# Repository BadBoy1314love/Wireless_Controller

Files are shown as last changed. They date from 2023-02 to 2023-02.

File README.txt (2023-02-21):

/*******************************************/
/         以下为程序思路整理
/*******************************************/

继电器任务应该由多个输入信号对应单个任务
继电器任务输出应该由单个任务输出一个或多个IO
而不是多个任务共同占用一个IO

一个任务：
输入触发信号（一个或者多个信号）--->启动指定的任务
--->输出一个或者多个信号（应该由一个任务占用这些输出信号）
（不能由其他任务占用这些输出信号）

设置项
首先设置触发信号
设置不同的IO触发任务号（每个IO有其对应的任务）

继电器任务模式：
1.点动模式：
	有触发信号（无松手检测），则有输出，否则没有
2.自锁模式：
	有带松手检测触发信号，则启动任务输出，
	再次触发，则关闭输出
3.时间区间间歇：
	有带松手检测触发信号，则启动任务输出，
	再次触发，则关闭输出
	可以设置时间区间
	可以设置输出ON的时间，可按百分比设置
	可以设置输出OFF的时间，可按百分比设置
	可以设置周期时间
	可以设置OVERTIME，任务运行超过此时间则关闭
	
	“间歇”：应该有三个要素（以秒（S）作为时间单位）
	运行的时间，停止的时间，总的时间（周期时间Cycle Time）
	_______________
	               |_______________
	|<--On Time -->|<--Off Time-->|
	|<--------Cycle Time--------->|
	
	应该确认什么时候开始运行也就是起始运行时间，
	得确认两个起始时间，一个是On状态的起始时间，还有一个是Off状态的起始时间
	一共有两个状态，一个是On状态，一个是Off状态
	在指定的时间区间内将状态设置为On或者Off
	也就是做时间区间内判断
	
继电器的任务输出：
	首先当前任务TASK1是启动的状态，并且有了一个输出
	通过这个输出结果TASK1_Out,值为1则输出已经为当前任务分配的IO
	值为0则不输出
	
为什么外部输入信号触发的是任务，而不是任务内的具体信号？
如果没有外部输入设备，则可以使用ec11内部的Start Task

任务的触发
1.自锁触发，按下按键，并且释放才触发，端口匹配的任务

自锁触发的过程
1.确认端口为输入模式并且为自锁模式且端口被拉低，则记录下端口
2.判断有哪些端口被记录，再次判断端口有没有被释放，被释放则用端口任务号赋给自锁任务号
3.匹配到自锁任务号则开启或者关闭匹配的任务

2.点动触发，按下按键，直接触发端口匹配的任务

按键为松开状态此时按下则记录

点动触发的过程
1.确认端口为输入模式并且按键为松开状态，端口被拉低，则直接记录下端口，按键状态变为按下
2.判断有哪些端口被记录，再次判断端口是不是点动触发型，
  是则立即将端口任务号赋给点动任务号，然后如果端口被释放，
  则将按键设置为松开状态，允许重新设置

自锁还是点动输入实际模拟外部输入
自锁：按下按键，记录下按下的按键，进入记录的按键，直到按键释放，才设置任务
立即：按下按键，直接设置任务，并且直到按键释放才可重新设置

任务的时间控制:
首先是判断当前时间在时间区间内
再判断超时计数器有没有大于超时时间

否则任务的运行不满足时间条件
1,当前时间不在时间区间内，没有超时
//当前关闭输出
//直到在时间区间，继续运行

2.当前时间不在时间区间内，已经超时
//如果开启超时自动复位，将复位计数,否则关闭task，复位时间计数器，关闭输出

3.当前时间在时间区间内，已经超时
//如果开启超时自动复位，将复位计数，否则关闭task，复位时间计数器，关闭输出

如果要实现无限时间运行（意味着超时自动复位）

/******************************************************************************/
// STA模式操作步骤
/******************************************************************************/

AT+CWMODE_DEF=3        //设置当前wifi模式并保存到flash /1:STA/2:AP/3.STA+AP
AT+CWMODE_CUR=3  //设置当前wifi模式不保存到flash

AT+CWJAP_DEF="wifiname","password"   //连接AP并保存到FLASH
AT+CWJAP_CUR="wifiname","password"   //连接AP不保存到FLASH

AT+CIFSR                    //查看路由器分配的IP

AT+CIPMUX=1         //设置多连接 

AT+CIPSERVER=1,9527   //设置TCP服务器 

/*STA+AP模式设置*/
AT+CWMODE_CUR=3
AT+CWJAP_CUR="TP-LINK_847A","asdfghjkl"
AT+CWSAP_CUR="Wireless_Controller_Test","asdfghjkl",11,4
AT+CIFSR
AT+CIPMUX=1
AT+CIPSERVER=1,9527

/*GET 苏宁时间网址*/（get网址之后一定要加、/r/n）
AT+CIPMUX=0
AT+CIPSTART="TCP","quan.suning.com",80
AT+CIPSTART="TCP","223.111.230.101",80
AT+CIPSEND=50
GET http://quan.suning.com/getSysTime.do

/*GET www.shijian.cc 网址的GMT+8标准时间 */（get网址之后一定要加、/r/n）
AT+CIPMUX=0
AT+CIPSTART="TCP","www.shijian.cc",80
AT+CIPSTART="TCP","118.112.250.193",80
AT+CIPSEND=50
GET http://www.shijian.cc/000/clock.asp

/*GET www.beijing-time.org 网址上的GMT+8标准时间*/（get网址之后一定要加、/r/n）
AT+CIPMUX=0
AT+CIPSTART="TCP","beijing-time.org",80
AT+CIPSEND=50
GET http://www.beijing-time.org/t/time.asp
GET http://beijing-time.org/t/time.asp

GET /t/time.asp

/*http://api.k780.com/?app=life.time&appkey=10003&sign=b59bc3ef6191eb9f747dd4e83c99f2a4&format=json
*/

/*ESP8266的其他指令*/

AT+CIPSEND

AT+RESTORE   //重置

/*设置 UART 配置，保存到 Flash*/
AT+UART_DEF(_CUR)=9600,8,1,0,0

/*8266的初始化过程*/

AT+RST    //复位8266模块
AT+CWMODE_CUR=3   //设置当前wifi模式  
AT+CWJAP_CUR="TP-LINK_847A","asdfghjkl"   //连接AP

/*获取网络时间*/
AT+CIPSTART="TCP","www.shijian.cc",80
AT+CIPSEND=42
GET http://www.shijian.cc/000/clock.asp\r\n\r\n
显示时间

AT+CIPMUX=1   //使能多连接
AT+CIPSERVER=1,9527  //开启TCP服务器，只能在多连接的情况下开启
AT+CWSAP_CUR=\"Wireless_Controller\",\"asdfghjkl\",3,4  //设置8266 SOFTAP
AT+CIFSR

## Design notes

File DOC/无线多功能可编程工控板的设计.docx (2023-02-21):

江苏省无锡交通高等职业技术学校

毕 业 论 文

无线多功能可编程工控板的设计

学 院 | 机电工程学院
专 业 | 机电一体化
班 级 | 161321
姓 名 | 张淼垚
学 号 | 160332014
指导教师 | 蒋甜
起讫日期 | XXXX.XX～XXXX.XX

无线多功能可编程工控板的设计

# 摘 要

进入21世纪后，互联网技术获得了飞速的发展，随着传感器技术的发展，物联网技术也相继而生。

人们的生活水平获得了极大的提高的同时，人们对生活的要求也相应的提高了，为了获得更加优质的生活，获得智能化的生活，人们采用了物联网技术来提高生活质量。为了实现多功能的物联网控制，为了极大的便利生活，在生活中解放双手，在家庭中实现通用控制。

受到工业中常用的稳定可靠的PLC的影响，为了设计一种稳定可靠的便于在家庭中使用的多功能无线控制器，本文将讲诉STC89C52RC单片机为核心的一种低成本、时间准时、小型化无线多功能可编程工控板的设计。

关键词：物联网，传感器，多功能通用，无线，控制器，PLC

# 第一章 物联网的介绍

## 1.1 物联网的定义

物联网是指通过各种传感器将万物互联的互联网，是在互联网的基础上发展而来，物联网是将各种信息传感设备与网络的相结合从而形成的巨大网络，实现了在任意时间，任意地点，人与物与机的互联互通。

## 1.2 物联网的工作原理

通过各种信息传感器，例如射频识别、红外传感、激光扫描、全球定位等各种装置，实现采集例如声、光、热、电、力等各种信息，通过网络连接，实现，物与物，物与人之间的连接，实现对物品的智能化识别管理，整个过程是智能化的。

## 1.3 物联网的益处

通过物联网可以获得的最大好处是能够提高社会的智能化，自动化的水平，把原来不能实现的难以实现的功能实现了。通过给没有智慧的物体植入无线智能芯片，让人类的的感知更加灵敏，更加宽广，使得控制更加自如，让生活更加方便。

# 第二章 传感元件及动力元件

## 2.1 传感器原理及应用举例

### 2.1.1 主动式红外传感器

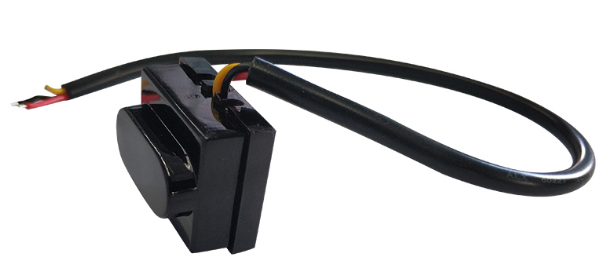
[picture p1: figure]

图2-1 主动式红外传感器实物图

主动式红外传感器是一种智能的非接触开关，利用红外光对物体的漫反射原理，当人或者物体进入感应器的感应区域，感应器将输出信号，人或物体离开后将停止输出，一般应用场景为水龙头阀门的感应开启与关断。

一般有高低电平输出方式以及NPN输出方式。

高低电平输出方式只提供一个高低电平信号，适用于小电流控制大电流，控制外部电路，MCU信号的识别与判断等，硬件连接示意图如图（2-2）。

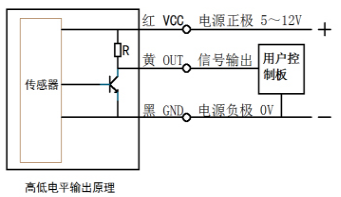
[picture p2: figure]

图2-2 高低电平原理图及接线图

NPN输出方式，当传感器输出断开时处于无电压的悬空状态，可以通过上拉电阻接到VCC的输出电压，当传感器输出闭合时电压为０V，即对０V（电源负极）导通，硬件连接示意图如图（2-3）。

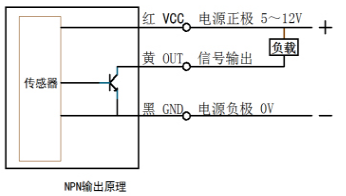
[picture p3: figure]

图2-3 NPN输出原理图及接线图

### 2.1.2 霍尔开关传感器

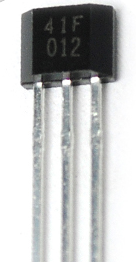
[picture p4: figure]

图2-4 霍尔开关传感器实物图

一般由电压调整器，霍尔电压发生器，差分放大器，施密特触发器，温度补偿电路和集电极开路的输出级组成的的磁敏传感电路，由半导体集成技术制造而成，一般输入为一个磁感应强度，输出是一个电压数字信号。

该传感器具有体积小，灵敏度高，响应速度快，温度性能好，精确度高，可靠性高等优点，应用场景一般为无触点开关，位置，转速检测与控制，报警装置。

### 2.1.3 光敏传感器

图2-5 光敏电阻器实物图

光敏电阻的工作原理是基于内光电效应。随着光照强度的升高，电阻值迅速降低，由于光照产生的载流子都参与导电，在外加电场的作用下作漂移运动，电子奔向电源的正极，空穴奔向电源的负极，从而使光敏电阻器的阻值迅速下降。在无光照时，几乎呈高阻状态，暗电阻很大。

基于光敏电阻器的工作原理于是有了光敏电阻传感器模块。

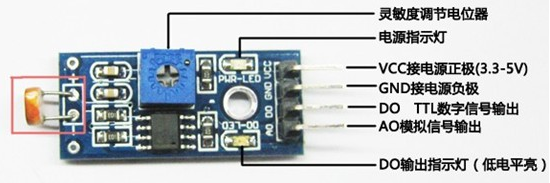
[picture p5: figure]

图2-5 光敏电阻传感器模块

光敏电阻传感器模块由光敏电阻，灵敏调节电位器，LM393宽电压比较器所组成，可以通过调节电位器来调节阈值输出电平，使得在光照强度达到阈值的情况下，DO端输出低电平，未达到时则为高电平。

光敏电阻传感器一般可以应用在电灯自动控制电路中，在电视机中一般做亮度自动调节。

## 2.2 动力原件原理及应用举例

### 2.2.1 电磁阀

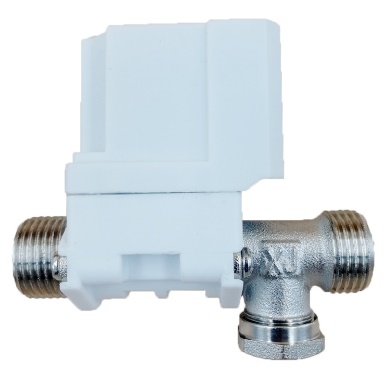
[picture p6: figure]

图2-6 直流电磁阀

电磁阀是用电磁 (https://baike.baidu.com/item/%E7%94%B5%E7%A3%81)控制的工业设备 (https://baike.baidu.com/item/%E5%B7%A5%E4%B8%9A%E8%AE%BE%E5%A4%87/7909654)，是用来控制流体的自动化基础元件，属于执行器，并不限于液压、气动。用在工业控制系统中调整介质的方向、流量 (https://baike.baidu.com/item/%E6%B5%81%E9%87%8F/1203080)、速度和其他的参数。电磁阀可以配合不同的电路来实现预期的控制，而控制的精度和灵活性都能够保证。

基本原理式是通电时，电磁线圈产生电磁力把关闭件从阀座上提起，阀门打开；断电时，电磁力消失，弹簧把关闭件压在阀座上，阀门关闭，实现了对流体的通断控制。

### 2.2.2 直流电动机

图2-7 小型直流电动机

直流电动机是一种可以将直流电能转换为机械能的转动装置。

一般组成是由定子和转子两大部分组成，直流电动机在运行时静止不动的部分称为定子，主要作用是产生磁场，在运行时转动的部分称为转子，主要作用时产生电磁转矩和感应电动势，运行时由直流电源来给转子上的绕组提供运行时所需要的电流，换向器使得转子电流与磁场产生的转矩方向保持不变，从而使转子发生机械旋转。

如图（2-7）所示的电动机的应用场合一般为，电动玩具，电动智能设备中，例如电动按摩椅，扫地机器人，吸尘器，电动玩具车等。

# 第三章 STC89C52RC单片机

## 3.1 STC89C52RC单片机的简介

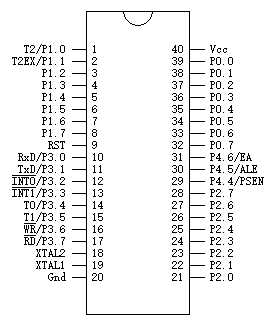
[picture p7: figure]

图3-1 STC89C52RC单片机管脚图

STC89C52是STC (https://baike.baidu.com/item/STC/4307113)公司生产的一种低功耗、高性能CMOS8位微控制器，具有8K字节系统可编程Flash存储器 (https://baike.baidu.com/item/Flash%E5%AD%98%E5%82%A8%E5%99%A8/1254787)。STC89C52使用经典的MCS-51内核，但是做了很多的改进使得芯片 (https://baike.baidu.com/item/%E8%8A%AF%E7%89%87/32249)具有传统的51单片机不具备的功能。在单芯片上，拥有灵巧的8 位CPU (https://baike.baidu.com/item/CPU%20/120556)和在系统可编程 (https://baike.baidu.com/item/%E7%BC%96%E7%A8%8B/139828)Flash，使得STC89C52为众多嵌入式控制应用系统提供高灵活、超有效的解决方案。

STC89C52RC具有以下标准功能:具有8K字节的Flash，512字节RAM，32个I/O口线，看门狗定时器，内置4KB的EEPROM，MAX810复位电路，3个16 位定时器 (https://baike.baidu.com/item/%E5%AE%9A%E6%97%B6%E5%99%A8)/计数器，4个外部中断，一个7向量4级中断结构（兼容传统51的5向量2级中断结构），一个全双工串行口 (https://baike.baidu.com/item/%E4%B8%B2%E8%A1%8C%E5%8F%A3)。另外STC89C52可降0Hz静态逻辑操作，支持2种软件可选择节电模式。空闲模式下，CPU 停止工作，允许RAM、定时器/计数器、串口、中断继续工作。掉电保护方式下，RAM内容被保存，振荡器被冻结，单片机一切工作停止，直到下一个中断或硬件复位为止。最高运作频率35MHz，6T/12T可选。

## 3.2 STC89C52RC单片机的内部结构

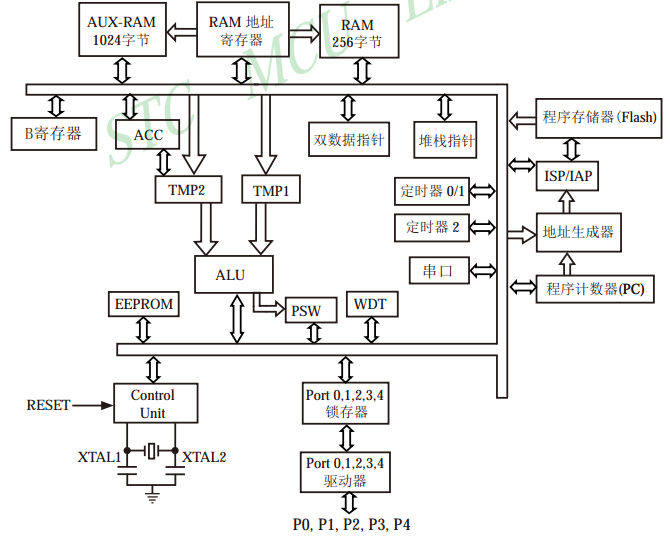
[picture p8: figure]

图3-1 STC89C52RC单片机内部结构图

STC89C52RC单片机的内部结构框图如图（3-1）所示，内部包含中央处理器（CPU），程序存储器（Flash），数据存储器（SRAM），定时/计数器，UART串口，I/O接口，

EEPROM，看门狗等模块。STC89C52RC单片机几乎包含了数据采集和控制中所需要的所有单元。

## 3.3 STC89C52RC单片机的IO结构与功能

STC89C52RC单片机所有IO口（包含新增的P4口）有三种工作类型：准双向口/弱上拉，仅为输入高阻或开漏输出功能。

其中P0口每个IO最大灌电流为12MA，其他IO的灌电流为６MA。

准双向口输出类型可用作输出和输入功能而不需重新配置端口输出状态。这是因为当端口输出为1时驱动能力很弱，允许外部装置将其拉低。当引脚输出为低时，它的驱动能力很强，可吸收相当大的电流。准双向口有3个上拉晶体管适应不同的需要，内部结构图如图（３-2）所示。

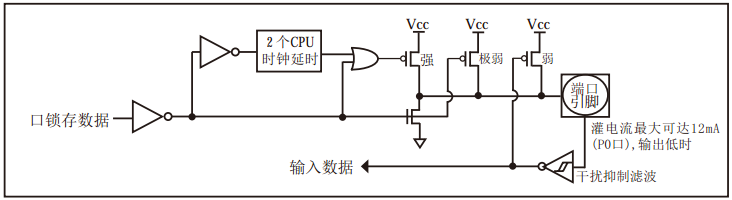
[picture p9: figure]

图3-２ STC89C52RC单片机准双向口输出内部结构图

P0口上电复位后处于开漏模式，当P0管脚作I/0口时，需外加10K-4.7K的上拉电阻，当P0管脚作为地址/数据复用总线使用时，不用外加上拉电阻。

当端口锁存器为0时，开漏输出关闭所有上拉晶体管。当作为-一个逻辑输出时，这种配置方式必须有外部.上拉，一般通过电阻外接到Vcc。如果外部有上拉电阻，开漏的I/0口还可读外部状态，即此时被配置为开漏模式的I/0口还可作为输入I/0口。这种方式的下拉与准双向口相同。输出端口配置如图（3-3）所示。

开漏端口还带有一个干扰抑制电路。

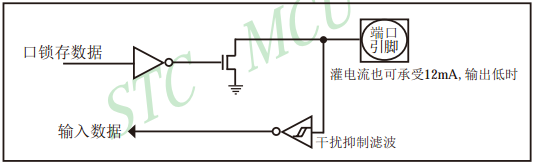
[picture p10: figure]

图3-２ STC89C52RC单片机开漏输出内部结构图

P0口：P0口是一个8位漏极开路的双向I/O口。作为输出口，每位能驱动8个TTL逻辑电平。对P0端口写“1”时，引脚用作高阻抗输入。当访问外部程序和数据存储器时，P0口也被作为低8位地址/数据复用。在这种模式下，P0具有内部上拉电阻。在flash编程时，P0口也用来接收指令字节;在程序校验时，输出指令字节。程序校验时，需要外部上拉电阻。

P1/P2口：P1/P2口是一个具有内部上拉电阻的8 位双向I/O 口，p1 输出缓冲器能驱动4个TTL逻辑电平。对P1 端口写“1”时，内部上拉电阻把端口拉高，此时可以作为输入口使用。作为输入使用时，被外部拉低的引脚由于内部电阻的原因，将输出电流拉低。

P3口：P3口是一个具有内部上拉电阻的8位双向I/O 口，P3输出缓冲器能驱动4个TTL逻辑电平。对P3端口写“1”时，内部上拉电阻把端口拉高，此时可以作为输入口使用。作为输入使用时，被外部拉低的引脚由于内部电阻的原因，将输出电流拉低。P3口亦作为STC89C52特殊功能(第二功能)使用。

第二功能为，P3.0 RXD(串行输入口)，P3.1 TXD(串 行输出口)，P3.2 INTO外中断0)，P3.3 INT1外中断1)，P3.4 TO定时/计数器0)，P3.5 T1定时/计数器1)，P3.6WR(外部数据存储器写选通，P3.7RD(外部数据存储器读选通)。

# 第四章 无线多功能可编程工控板的设计

## 4.1 无线多功能可编程工控板的设计要求

本无线多功能可编程工控板要求：

1. 电源兼容5V USB接口充电头。
2. 使用STC89C52RC单片机作为主控芯片。
3. 输入输出级有光耦光电隔离，输入输出级均有信号指示灯，输出级还可以任意端口切换大功率晶体管与继电器输出。
4. 具有DB9串口通信接口电路进行串口通信，具有ESP8266无线串口模块进行无线串口通信，USB接口可以下载调试程序且同时可以进行串口通信，串口不同的模块要能够关闭和开启，同时在通过串口通信时要具有指示灯。
5. 具有EC11编码器可以对工控板进行基本的功能选择，基本的交互功能。
6. 具有LCD1602液晶屏幕进行信息显示，LCD1602要能够对显示对比度，以及显示亮度进行调整
7. 板载一个无源蜂鸣器用于报警提示等。
8. 具有ISP下载接口，兼容AT系列单片机。

综上所述，整个工控板首先应当具有极高的可靠性以及兼容性，具有多种功能且要能进行无线通信，可编程升级程序。

## 4.2 无线多功能可编程工控板的总体方案

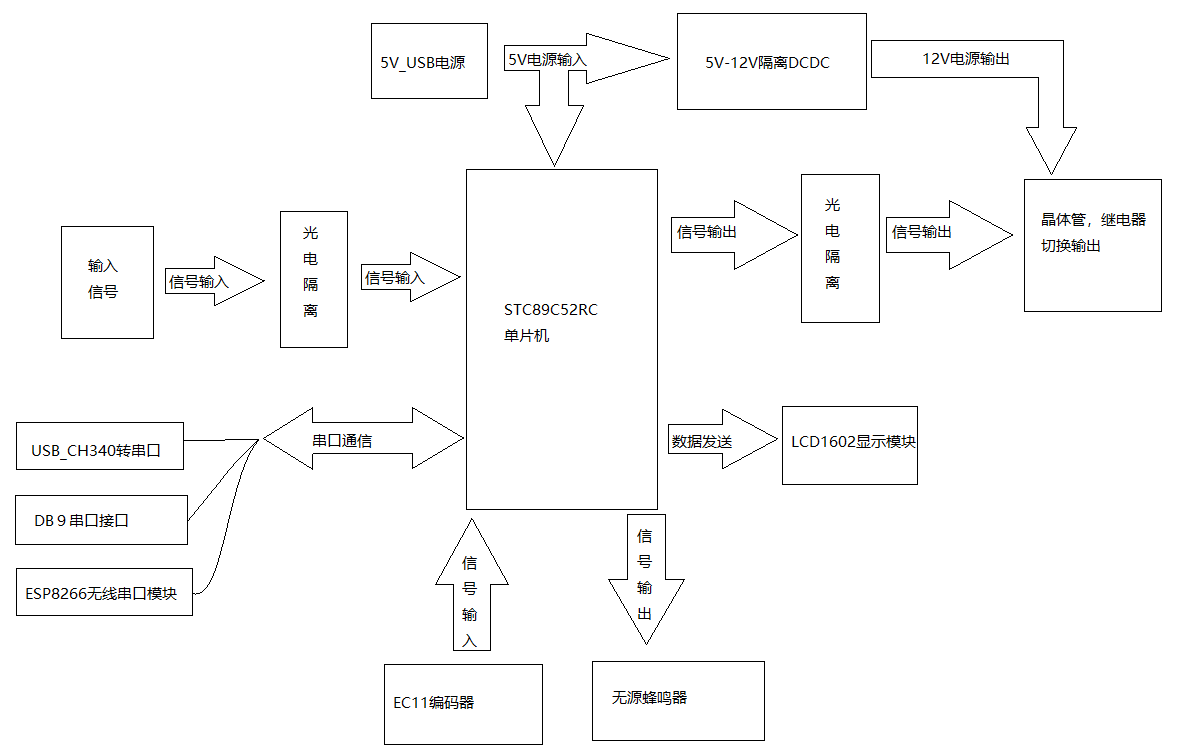
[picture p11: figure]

图4-1 无线多功能可编程工控板结构框图

如（4-1）图所示，无限多功能可编程工控板由STC89C52RC单片机，电源模块，光电隔离输入级电路，光电隔离输出级电路，LCD1602显示模块，EC11编码器输入，无源蜂鸣器报警输出，多功能串口通信模块部分所组成。

该工控板的系统中USB输入级电源还使用了钮子开关4线有效关断，输出级电路使用DCDC5V-12V隔离电源模块电路进行供电，输出级晶体管与继电器是前后级关系，使用钮子开关进行输出切换，输入输出级均使用光耦进行光电隔离，串口部分的模块电路每个部分与串口相接的位置均使用了一个自锁开关用于选通各个功能，串口模块电路中的ESP8266可以进行无线通信以及远程控制，此外还有EC11编码器作为信号输入，无源蜂鸣器进行响应，LCD1602显示模块，共同构成了简单的人机交互。

综上所述，此无线多功能可编程工控板实现了无线多功能可编程的控制。

## 4.3 无线多功能可编程工控板的硬件电路设计

### 4.3.1 单片机最小系统的设计

单片机最小系统，一般也叫做单片机最小应用系统，是指用最少的元器件组成的单片机可以工作的系统，单片机最小系统就是由单片机，电源，晶振、复位电路所组成。

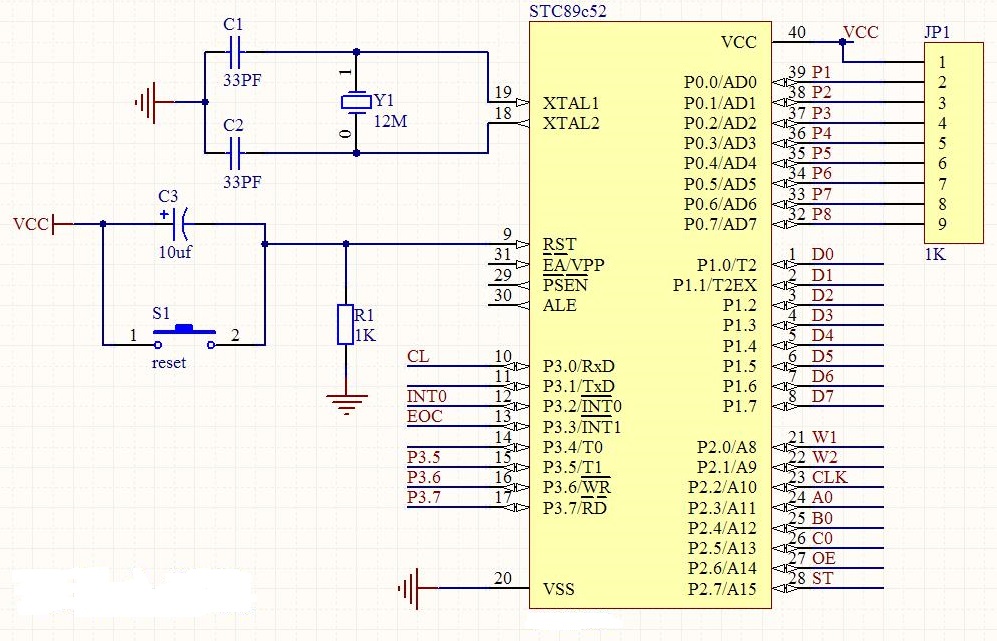
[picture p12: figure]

图4-2 单片机最小系统

如（4-2）图所示，此为单片机的最小系统。

1. 电源电路：STC89C52RC的供电范围为4.5V至5.5V，一般电源供电电压选择为5V。
2. 复位电路：具有上电自动复位以及手动复位，图上为RC阻容复位，在上电时，由于电容两端电压不能突变，在电容未充满电之前可视为导线，这样就相当于将电源VCC直接接入了RST复位引脚，RC的乘积决定了充放电的快慢，STC89C52RC单片机复位时，一般只要在RST引脚上维持两个机器周期以上的高电平即可实现复位
3. 晶振电路（时钟电路）：如图所示的晶振电路可以提供一个稳定的振荡频率，为12MHz，为单片机提供了精确的时钟。

### 4.3.2 输入级电路的设计

输入级电路的基本要求是要有输入指示灯，光耦隔离。

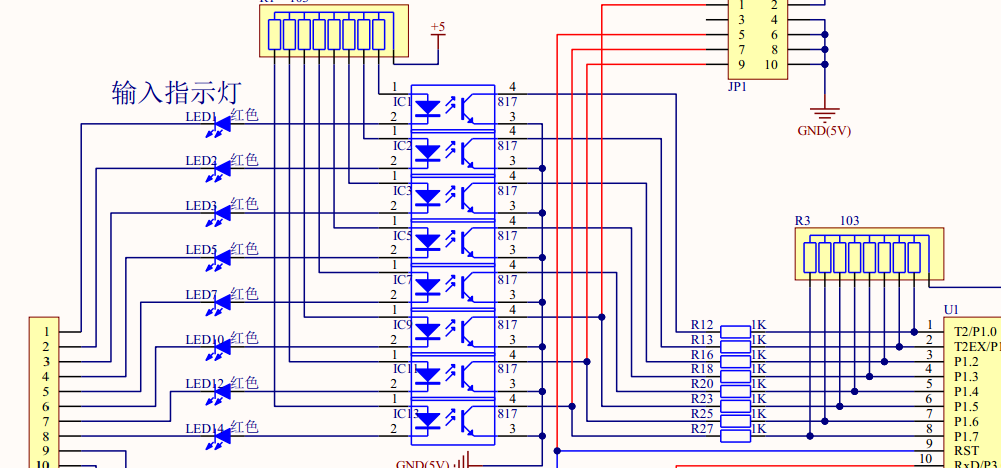
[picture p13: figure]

图4-3 无线多功能可编程工控板输入级电路

如图（4-3）所示的无线多功能可编程工控的输入级电路，接入传感器时一般输入为低电平有效，可以直接接开关或者按钮，光耦隔离使用PC817，输入端电流一般控制在5-20MA时可稳定工作，该电路设计的标称值为10MA，输入端串接输入指示灯导通压降为1.2V，光耦输入级相当于一个LED导通压降大约为1.2V，所以输入限流电阻的阻值则为（5V-1.2V-1.2V）／10MA=260Ω，一般选用220Ω的电阻同样可以满足使用，光耦输出级导通之后单片机IO被拉低，信号输入单片机。

### 4.3.3 输出级电路的设计

输出级电路的基本要求是要有输出指示灯，光耦隔离，输出可以通过钮子开关进行晶体管与继电器的切换输出。

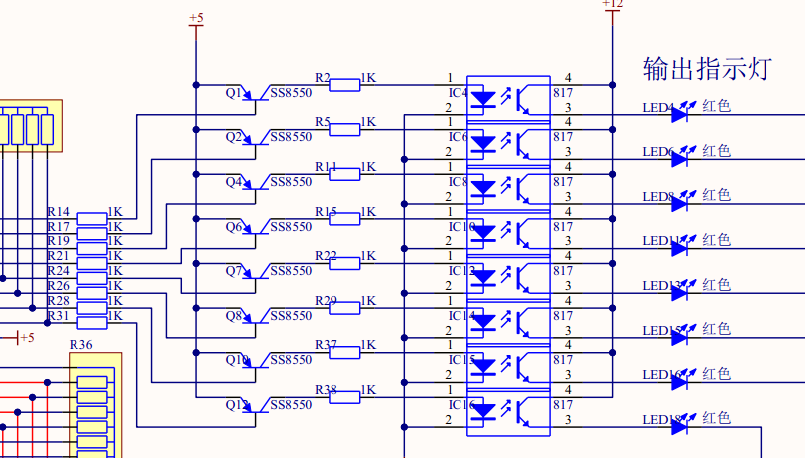
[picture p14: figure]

图4-4 无线多功能可编程工控板输出级电路光耦隔离电路

如图（4-4）所示的是无线多功能可编程工控板输出级电路中的光耦隔离部分，为了保证光耦可靠的导通，光耦输入级使用ss8550PNP三极管饱和导通通过330Ω限流电阻限制输入级电流为11MA，光耦输出端串接红色输出指示灯，电路工作正常时发红色光，输出端电路损坏时则不发光。

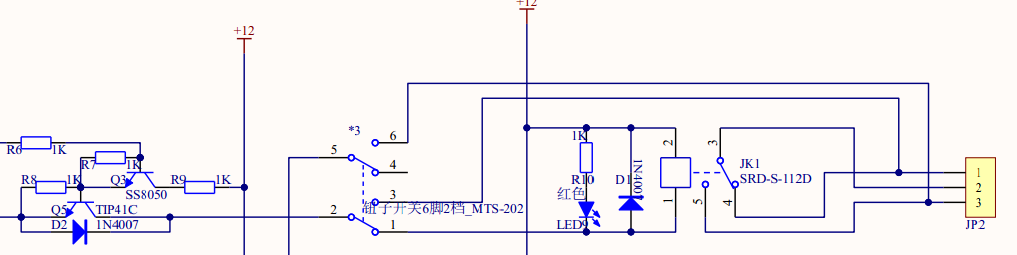
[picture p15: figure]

图4-5 无线多功能可编程工控板输出级电路晶体管/继电器切换电路

如图（4-5）所示的是无线多功能可编程工控板输出级电路中的晶体管/继电器切换电路。继电器工作时，继电器的前级使用了由小功率SS8050晶体管，TIP41C大功率NPN晶体管所组成的达林顿结构的放大电路TIP41C工作在饱和导通状态，使得继电器的线圈导通，继电器线圈还并接了红色的LED串接电阻用于继电器导通指示，还反向并接了1N4007作为续流二极管，保证前级元件不受反向电动势的影响，拨动钮子开关可以将继电器输出切换到晶体管输出，端子排上接晶体管的集电极和发射极，同时也反向并接了1N4007，一般外部接入感性负载，如电动机，或者继电器时，作为续流二极管。

### 4.3.4 LCD1602液晶显示电路

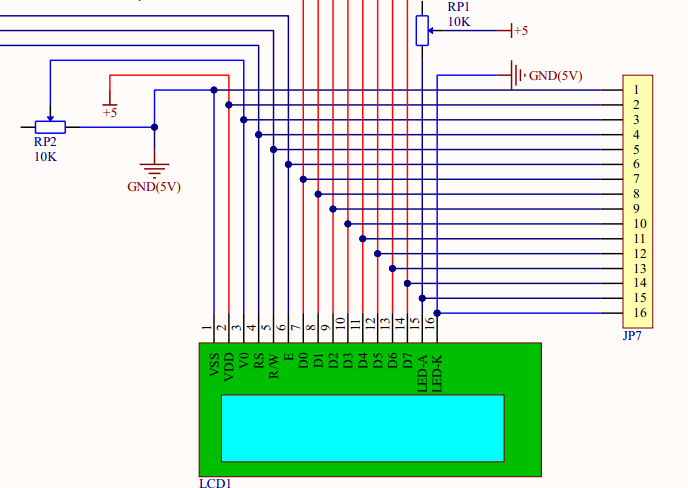
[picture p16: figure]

图4-6 无线多功能可编程工控板LCD1602液晶显示电路

如图（4-6）所示的是LCD1602液晶显示电路，V0端串接一个10k的精密可调电阻用于调节显示对比度，在LED背光源的部分也串接了一个可调电阻用于调节显示亮度，IO均接在单片机上用于控制以及数据写入。

### 4.3.5 EC11编码器电路

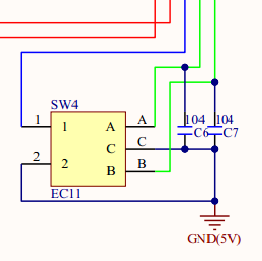
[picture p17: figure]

图4-7 EC11编码器电路

如图所示的是EC11编码器电路，1端接在INT0（P3.2）管脚上用于进入中断程序进行模式的切换，功能的选择以及设置。AB相接在P3.3与P3.4上同时两相与地之间各并联了一个高频电容用于滤除杂波，实现了更加稳定可靠的信号输出。

### 4.3.6 无源蜂鸣器电路

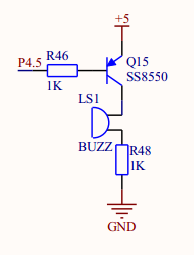
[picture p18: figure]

图4-8 无源蜂鸣器电路

如图所示的是无源蜂鸣器电路，使用SS8550_PNP三极管对输入电流进行放大来稳定驱动无源蜂鸣器。

### 4.3.7 USB转串口CH340电路

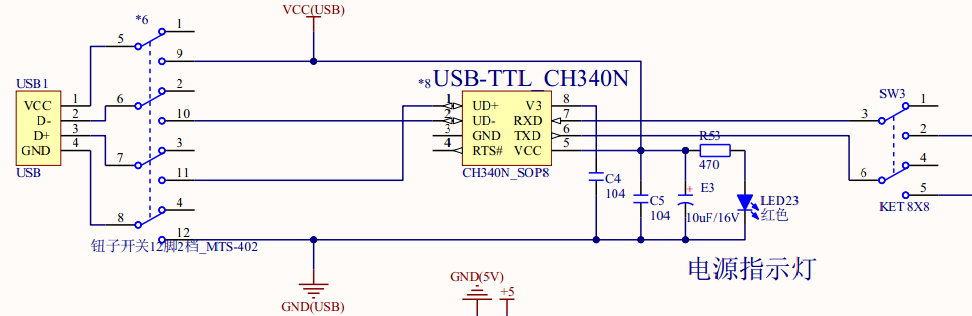
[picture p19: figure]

图4-9 USB转串口CH340电路

如图所示的是USB转串口CH340电路，USB端口用了一个4路妞子开关对4线的USB进行可靠关断，同时可将整个系统的电源可靠关闭，CH340N芯片旁边还有一个红色的电源指示灯用于显示电源的接通与断开，钮子开关拨通，红色电源指示灯亮起，钮子开关关断，红色电源指示灯熄灭。USB转串口芯片CH340N的RXD与TXD通过自锁开关接到单片机的TXD与RXD上，可以选择使用CH340N通信或者不通信。

### 4.3.8 DB9接口串口电平转换电路

由于工业上时常使用DB9接口作为串口通信的接口，所以本板也兼容此接口。

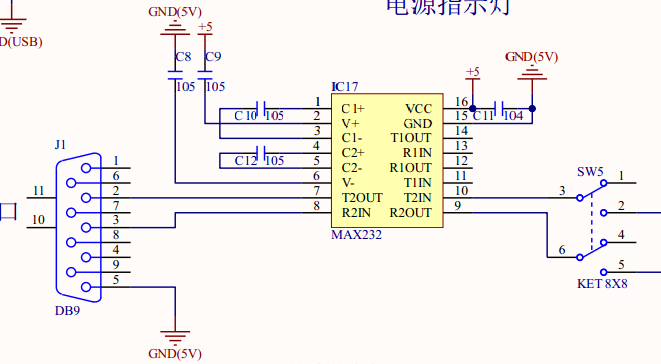
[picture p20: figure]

图4-10 DB９接口串口电平转换电路

如图所示的是DB9接口串口电平转换电路，一般计算机或者工业设备使用的电平为RS232电平，不兼容单片机电平，所以要使用MAX232电平转换IC对RS232电平进行转换为TTL电平，使之可以与单片机直接通信，不会损害单片机，同样此处的串口转换输出也是经过自锁开关与单片机RXD，TXD端口交叉连接。

### 4.3.9 ESP8266无线串口模块接口电路

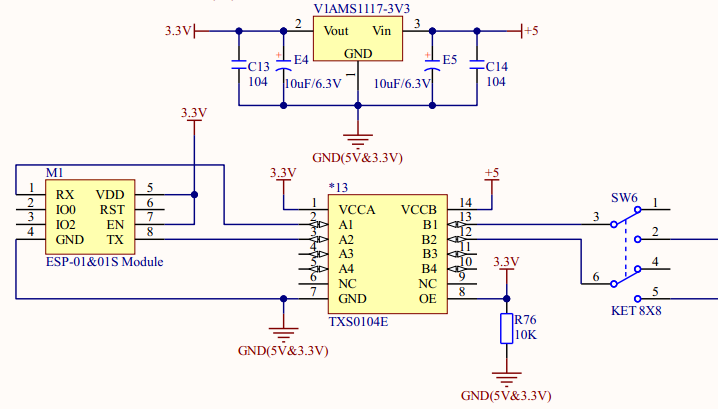
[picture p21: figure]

图4-11 ESP8266无线串口模块接口电路

如图所示的是ESP8266无线串口模块接口电路，由于ESP8266串口模块所使用的为3.3V的电压，所以单片机的5V电源供电不能直接使用，时间过长之后会烧坏模块，所以必须要使用电平转换，这里使用的是AMS1117稳压器将5V电源转换为3.3V电源供给ESP8266模块，为保证串口电平也相应的转换这里选择是哟个TXS0104E作为通信电平转换，使用非常方便，TXS0104E输出端同样经过自锁按钮接到单片机的串口，进行无线通信。

### 4.3.10 串口通讯指示电路

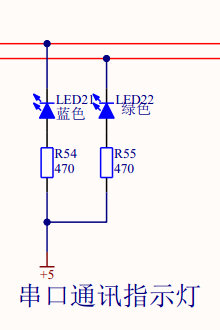
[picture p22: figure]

图4-12 串口通讯指示灯电路

如图所示的是串口通讯指示灯电路，主要作用是显示串口模块电路的通讯指示，

LED通过哟个470Ω的电阻接到串口线上，当串口电平发生变化时，通讯指示灯则会发生闪烁。

### 4.3.11 5V-12V DCDC隔离电源

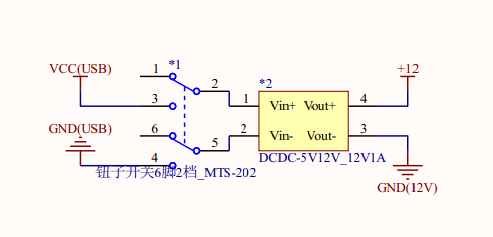
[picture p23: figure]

图4-13 5V-12 VDCDC隔离电源

如图所示，该模块一般使用时可以将5V电源升压至12V供给晶体管以及12V继电器使用，该模块可以使用一个妞子开关将输入电源关闭，实现断电。

### 4.3.12 ISP下载接口

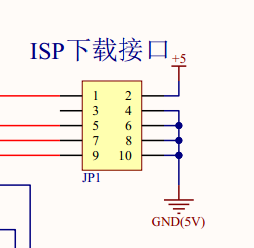
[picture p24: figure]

图4-14 ISP下载接口

如图所示的是ISP下载接口，用于兼容ATMEL的部分芯片比如AT89S52，在RST引脚处在高电平的情况下，利用P1.5/MOSI(串行数据输入端)，P1.6/MISO(串行数据输出端)，P1.7/SCK(同步时钟信号输入端)三个引脚的数据设置或传送实现程序下载的功能。

## 4.4 总结

经过硬件电路的设计，无线多功能可编程工控板成功的实现了，提高家庭中智能化的程度，实现了家庭中的自动化的水平，让原本无法实现的实现了，实现了对物的互联互通，让人类的的感知更加灵敏，更加宽广，使得控制更加自如，让生活更加方便。

# 参 考 文 献

# （一级标题，黑体，加粗，三号，字间空一个字符，居中，间距：段前、段后各1行，行距：1.5倍，参考文献至少列出10个）

空一行

[1] 杨瑞林, 李力军. 新型低合金高强韧性耐磨钢的研究. 钢铁. 1999（7）：41~45.

（期刊：序号 作者，题名，刊名，出版年份，卷号(期号)，起止页码）

[2] 温诗铸. 摩擦学原理. 北京：清华大学出版社. 1990：296-300.

（专著：序号 作者，书名，版本(第１版不标注)，出版地，出版者，出版年，起止页码）

[3] 贾名字. 工程硕士论文撰写规范[硕士论文].上海:上海交通大学. 2000.

毕业论文：序号 作者，题名，［毕业论文］，保存地点，保存单位，年份

# 致 谢

在学校度过了几年的时光，系统的学习了专业的各个部分的知识，我深深的佩服各位专业老师的学识，从中我不仅仅学到了专业的知识，而且也学到了很多做人做事的道理，教会了我如何学习，授人以鱼不如授人以渔。

在此我要感谢机电工程学院机电一体化的所有老师，你们无私的奉献精神和爱岗敬业的治学态度，也让我对专业有了更进一步的理解，将理论与实际相结合，受益匪浅，能够将所学知识应用到对现实生活中的实际问题解决，进而又提高了自己的专业水准。

本次设计的无线多功能可编程工控板，为了向着万物互联而设计，

将智能化，自动化向生活中传递，让人们的生活更加便利，能为社会做出一些贡献也是其意义所在。

在最后，我感谢所有曾经帮助过我的人，我将更加努力创造出更加智能化，自动化的作品，为社会创造价值。

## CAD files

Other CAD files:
CODE/Output/Main.obj
CODE/Output/Download.obj
DXF/Wireless_Controller_V1.1.dxf
CODE/Output/EEPROM.obj
CODE/Output/Sch51.obj
CODE/Output/LCD1602.obj
CODE/Output/LCD1602_Menu.obj
CODE/Output/UART.obj
CODE/Output/Timer.obj
CODE/Output/Relay.obj
CODE/Output/LCD1602_Show.obj
CODE/Output/Buzzer.obj
CODE/Output/LCD1602_Clock.obj
CODE/Output/EC11.obj
CODE/Output/ESP8266.obj
CODE/Output/Delay.obj
CODE/Output/EEPROM_Application.obj
CODE/Output/hSch51.obj

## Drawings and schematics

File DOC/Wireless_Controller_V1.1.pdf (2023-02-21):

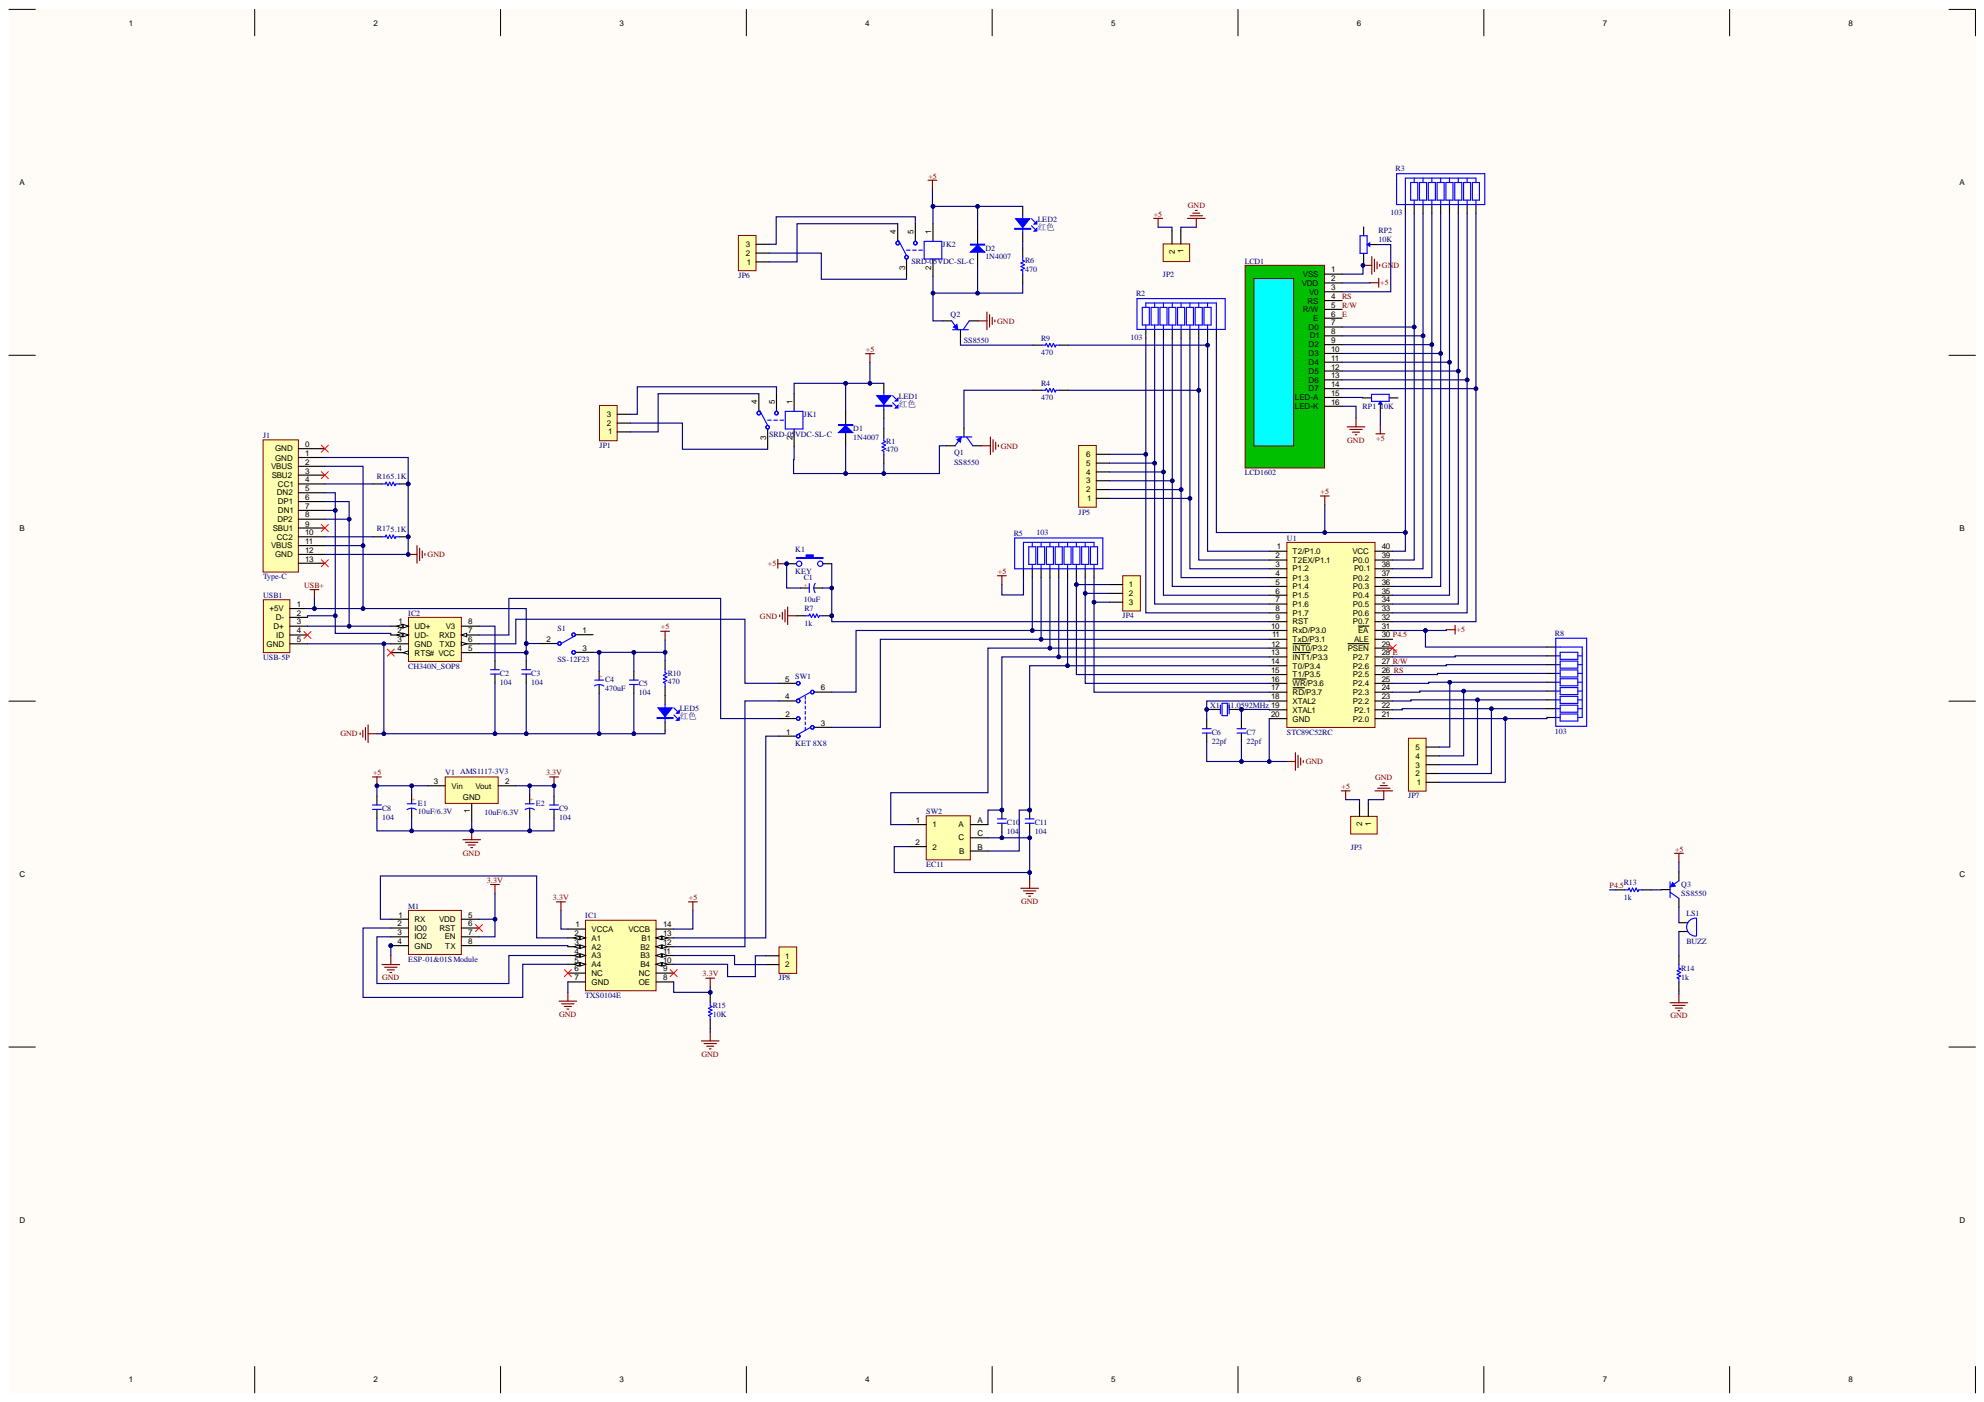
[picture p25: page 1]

INT1/P3.3 13
T0/P3.4 14 | R/W
T1/P3.5 15 | RS
WR/P3.6 16

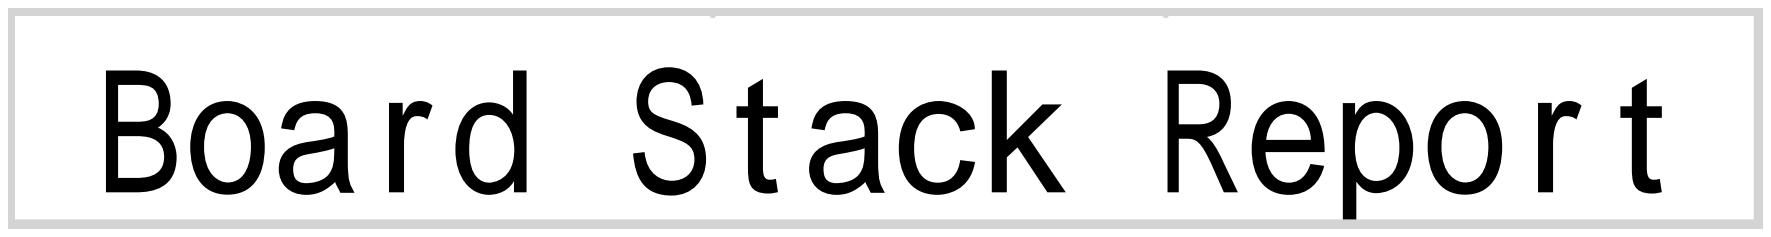
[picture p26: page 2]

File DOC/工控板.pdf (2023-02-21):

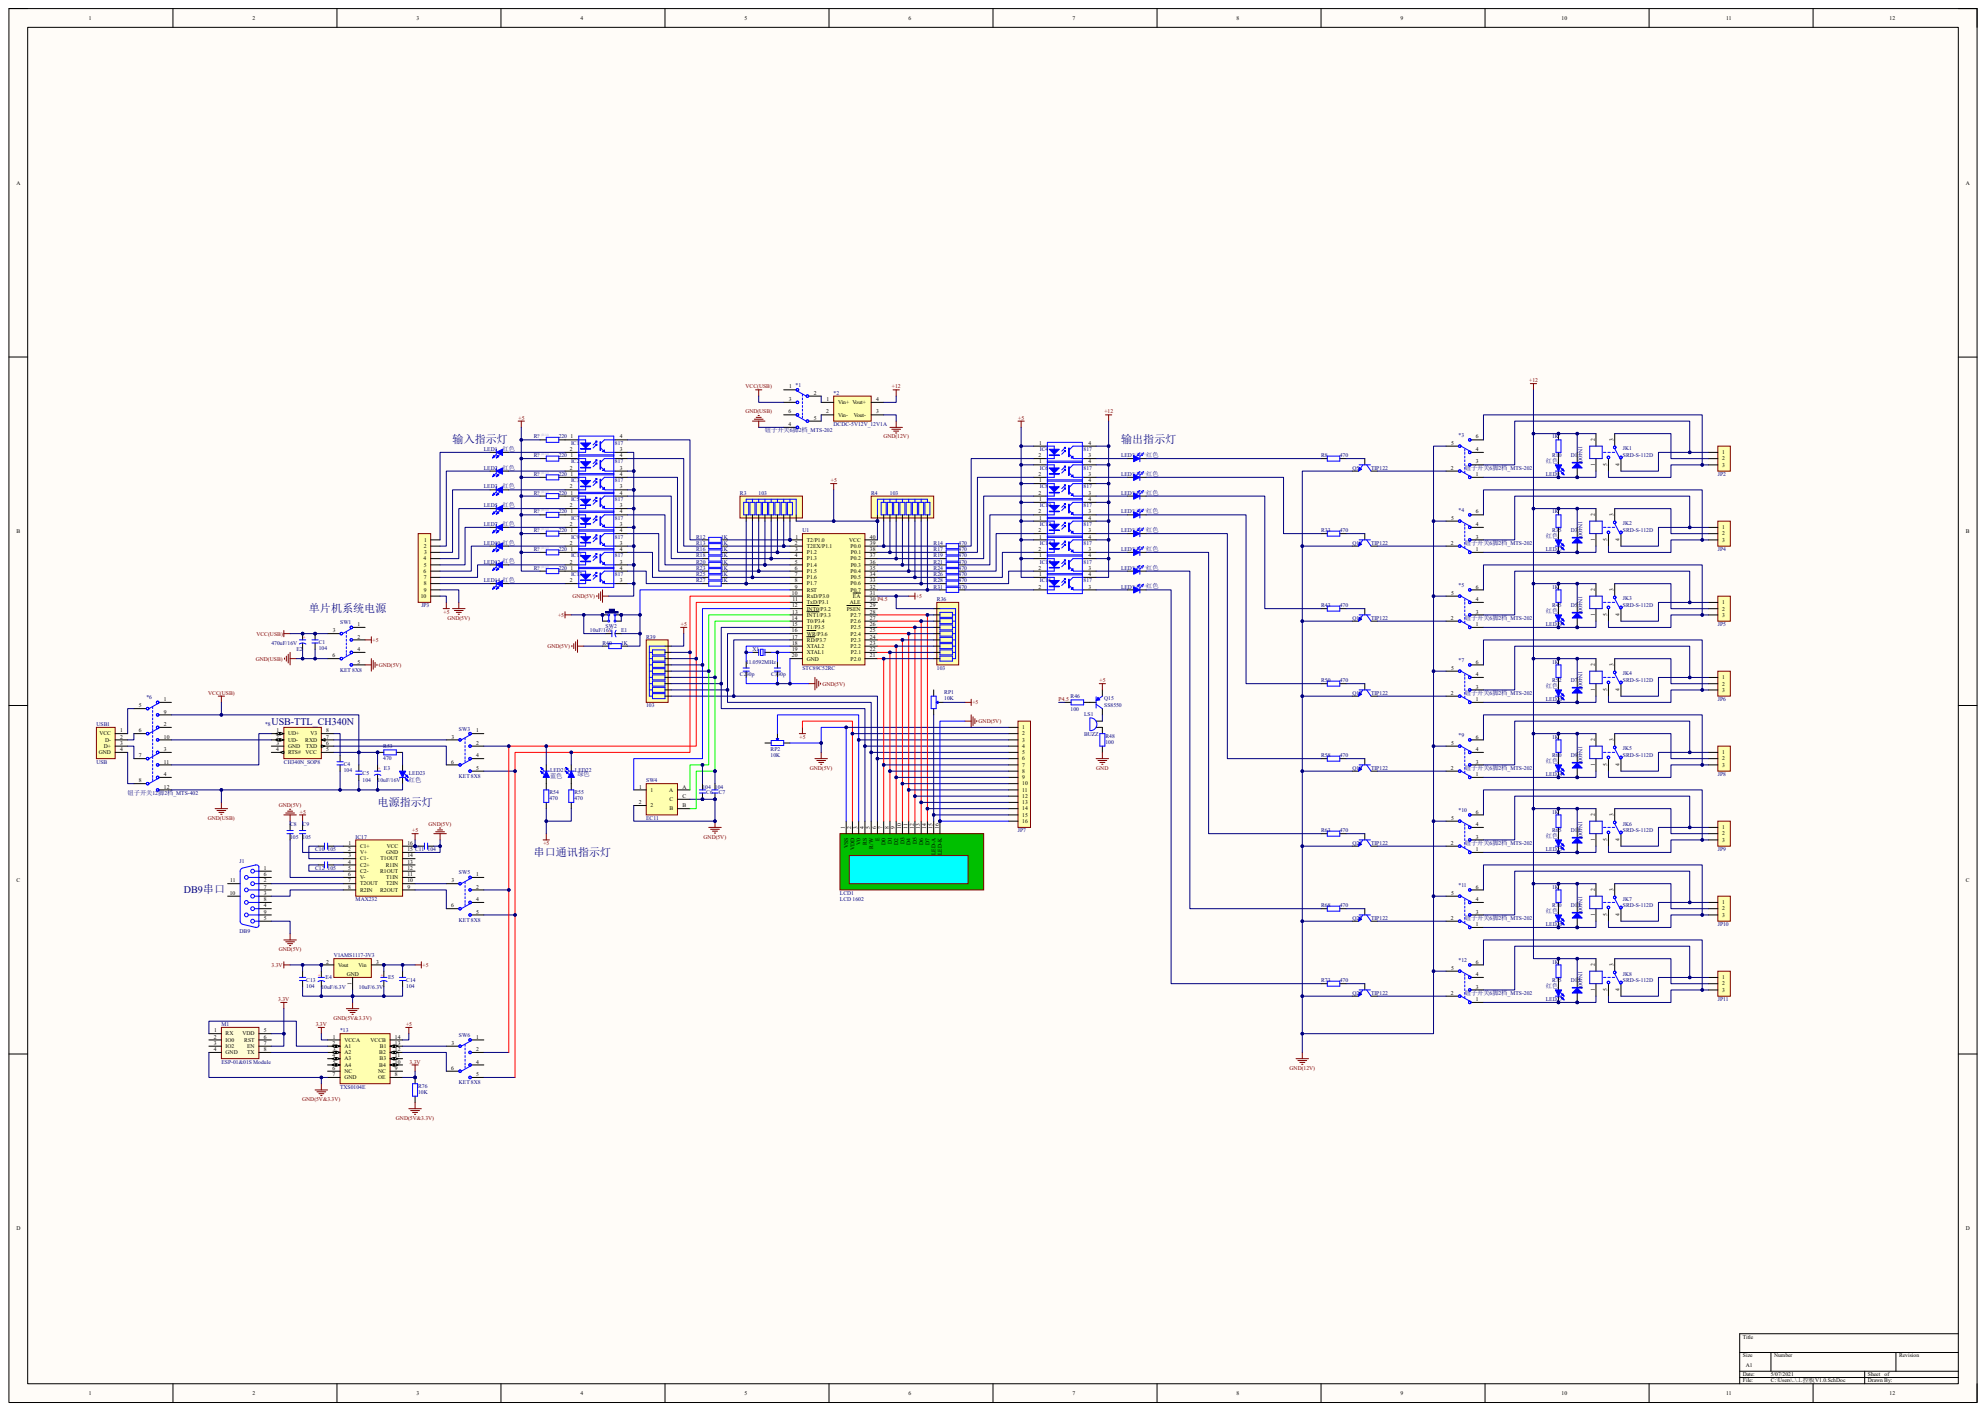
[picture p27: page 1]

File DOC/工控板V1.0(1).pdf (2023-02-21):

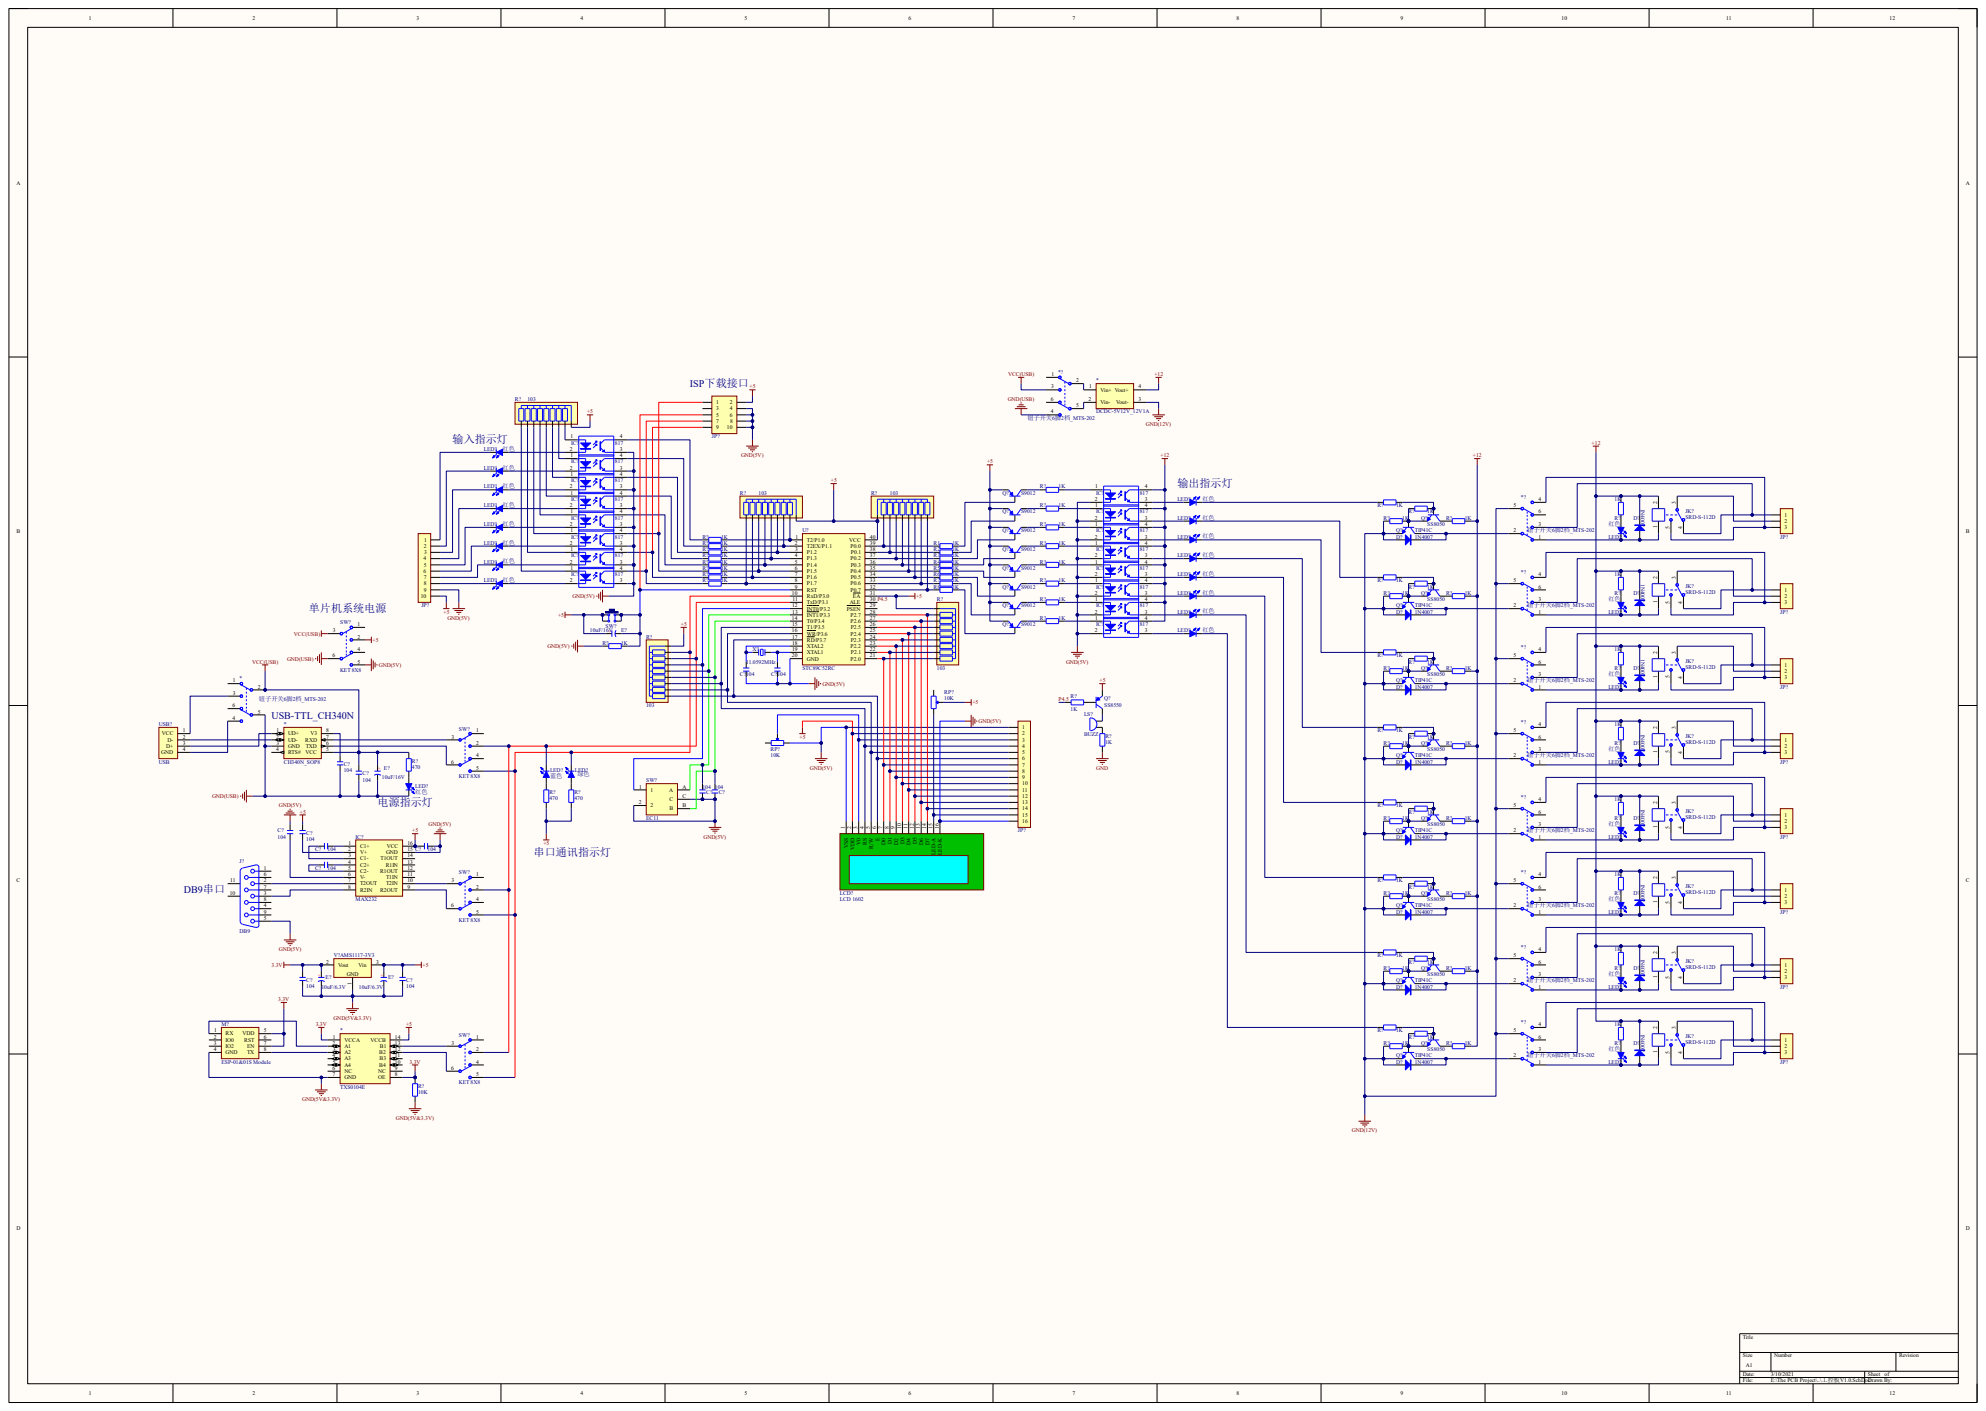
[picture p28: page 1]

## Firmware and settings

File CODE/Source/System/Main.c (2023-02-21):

/******************************************************************************/
// 包含头文件
/******************************************************************************/
#include "Config.h"
#include "LCD1602.h"
#include "LCD1602_Clock.h"
#include "LCD1602_Menu.h"
#include "LCD1602_Show.h"
#include "Timer.h"
#include "hSch51.h"
#include "Download.h"
#include "Relay.h"
#include "EEPROM.h"
#include "EEPROM_Application.h"
#include "EC11.h"
#include "Buzzer.h"
#include "UART.h"
#include "ESP8266.h"

/******************************************************************************/
// 定义变量
/******************************************************************************/


/******************************************************************************/
// main函数
/******************************************************************************/
int main(void)
{	
	/*初始化函数*/	
	
	P4SW = 0x20;   // 0010 0000
	P4M1=0xDF;  // 1101 1111
	P4M0=0x20;  // 0010 0000
	
	EEPROM_Read_Sector_1();
	Lcd1602_Init();
	EC11_Init();
	Timer1Init();
	Buzzer_Init();
	UartInit();  //初始化选择独立波特率发生器,启用串口中断
	
	hSCH_Start(); // 启动调度程序（开启总中断）
	
	Esp8266_STA_AP_Mode();  
	
	Lcd1602_Write_Cmd(0x01);//显示清屏
	
	hSCH_Init_T0(); //设置调度程序,初始化调度器，设置定时器0
									//为16位手动重装模式，定时1ms作为调度器时标
	
	hSCH_Pause();  //禁用用作为调度器时基的T2中断
	
	
	/*添加调度器任务*/
	hSCH_Add_Task(EC11_Scan,  0, 5 ,0);
	
	hSCH_Add_Task(LCD1602_Show_Update,  5, 100 ,1);
	hSCH_Add_Task(LCD1602_Time_Update, 40, 991 ,0);

  hSCH_Add_Task(Task_Input_Update,   51, 49 ,0);
	hSCH_Add_Task(Task1_Output_Update, 52, 49 ,0);
	hSCH_Add_Task(Task2_Output_Update, 53, 49 ,0);
	hSCH_Add_Task(Task3_Output_Update, 54, 49 ,0);
	
	hSCH_Add_Task(Task4_Output_Update, 55, 49 ,0);
	hSCH_Add_Task(Task5_Output_Update, 56, 49 ,0);
	hSCH_Add_Task(Task6_Output_Update, 57, 49 ,0);

//	hSCH_Add_Task(Buzzer_Open,  55, 500 ,1);
	
  hSCH_Run();  //启用作为调度器时基的T2中断
	
	
	
	/*主循环*/
	while(1)
	{
		hSCH_Dispatch_Tasks();
  }
}

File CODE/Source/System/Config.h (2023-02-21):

/******************************************************************************/
// 包含头文件
/******************************************************************************/
#include "STC12C5A60S2.H"
#include "intrins.h"

/******************************************************************************/
// 类型定义
/******************************************************************************/
typedef unsigned char u8; //0 to 255
typedef unsigned int  u16;  //0 — 65535
typedef unsigned long u32;   //0 — 4294967295

typedef unsigned char uint8;
typedef unsigned int  uint16;
typedef unsigned long uint32;
typedef signed char   int8;
typedef signed int    int16;
typedef signed long   int32;

typedef unsigned char tByte;
typedef unsigned int  tWord;
typedef unsigned long tLong;

typedef unsigned char BYTE;
typedef unsigned int  WORD;

typedef signed char		s8;  //–128 to 127
typedef signed int		s16;  //-32768 — 32767
typedef signed long		s32;  //-2147483648 — 2147483647


#define INTERRUPT_Timer_0_Overflow 1
#define INTERRUPT_Timer_1_Overflow 3
#define INTERRUPT_Timer_2_Overflow 5

#define INTERRUPT_EXTERNAL_0 0
#define INTERRUPT_EXTERNAL_1 2
#define INTERRUPT_UART_Rx_Tx 4

#define  ENABLE   1
#define  DISABLE  0

/******************************************************************************/
// LCD1602引脚配置
/******************************************************************************/
sbit RS = P2^5;
sbit RW = P2^6;
sbit EN = P2^7;
#define lcdPort P0 //LCD1602双向数据端口

/******************************************************************************/
// 继电器引脚配置
/******************************************************************************/
sbit RelayA = P1^0;
sbit RelayB = P1^1;

/******************************************************************************/
// EC11编码器引脚配置
/******************************************************************************/
sbit EC11_Key = P3^2;
sbit EC11_A = P3^3;
sbit EC11_B = P3^4;

/******************************************************************************/
// 无源蜂鸣器引脚配置
/******************************************************************************/
sbit Buzzer = P4^5;
